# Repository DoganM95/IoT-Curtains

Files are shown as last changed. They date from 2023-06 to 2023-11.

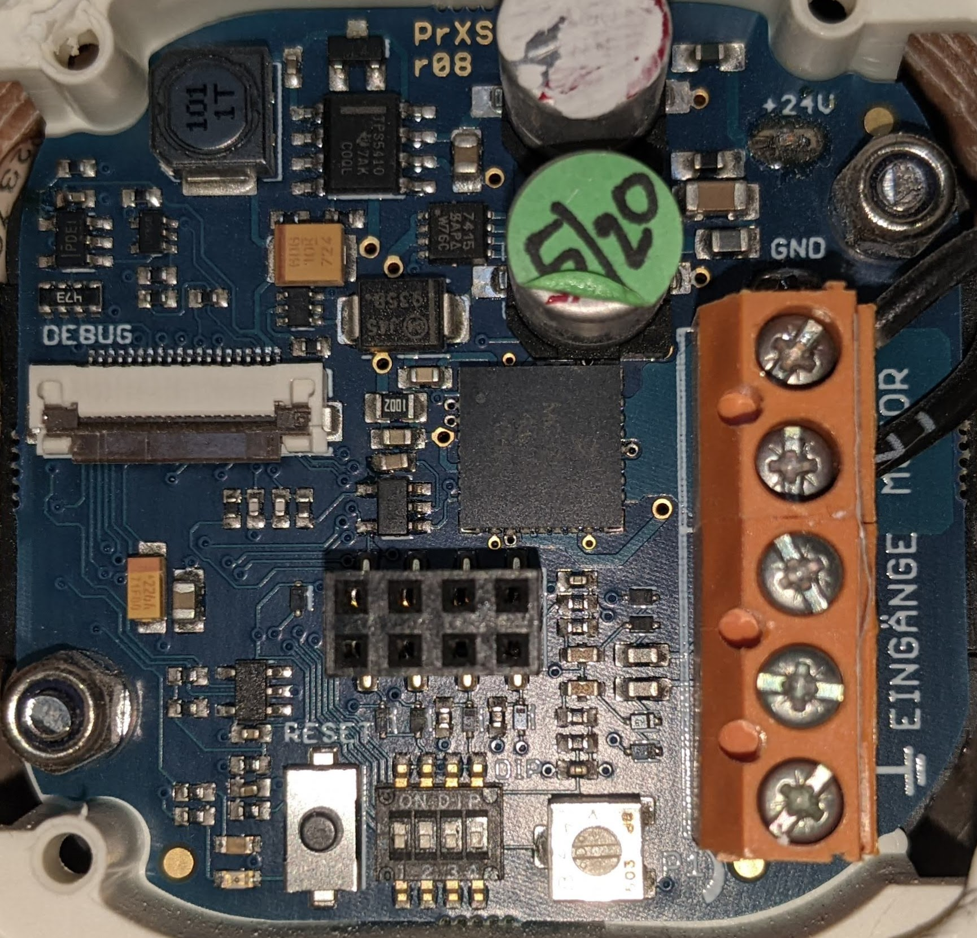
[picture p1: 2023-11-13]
Hardware/assets/wallmodule.png

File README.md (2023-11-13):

# IoT-Curtains
Outer facade electric curtains controlled by an esp32/arduino using Blynk
### Curtain controller pcb (wall module below)

- Pinout of screw spots:  

    Pin 5: Motor  
    Pin 4: Motor  
    Pin 3: close curtains  
    Pin 2: open curtains  
    Pin 1: GND  

- shorting pin 1 and pin 2 opens the curtains  
- shorting pin 1 and pin 3 closes the curtains  
- Pinout of female header pins (Wall side):

#### Power

The wall pcb provides power, rated at 3.3 Volts, but drops with increasing current draw.
The esp32 can be powered with a voltage between 2.2V and 3.6V and supposedly draws max 0.26A (Wifi Tx).
The following table contains measurements of voltage, respective to the current drawn at that moment.

<table>
  <tr>
    <td width="30%">
- 0.0A -> 3.31V<br/>  
- 0.1A -> 3.13V<br/>  
- 0.2A -> 2.93V<br/>  
- 0.3A -> 2.74V<br/>  
- 0.4A -> 2.55V<br/>  
- 0.5A -> 2.37V<br/>      
    </td>
    <td width="50%">USB-C PCB Bottom View</td>
  </tr>
</table>

### Hardware setup

- Shorting pins (1 and 2) && (1 and 3) by esp32 happens using AO3401A or AO3400A Mosfet, where esp controls the gate
- Mosfet Gate is connected to esp32 gpio (open/close)
- Mosfet gate is pulled down using a 10 kOhm resistor, connected from gate to ground
- pin 1 is connected to each Mosfet Source/Drain, depending on the diode direction of your mosfet (compare the 2 above in datasheets)
- pin 2/3 are each connected to a Source/Drain
- gpio will be high for a short time (e.g. 0.5s) to simulate a human button press

#### Existing wall module
This is the controller board that is built in to the wall. The wires of the motors of the facade are routed trough the wall and connected to it using the screw terminals. This module stays as is.
<table>
  <tr>
<td width="50%">Wall module</td>
    <td width="50%">Wall module labeled</td>
  </tr>
</table>

#### Preview of retrofitting smart module
This is the smart-module built in this project, which attaches to the wall-module above. It replaces the simple stock pcb that was attached to the wall module by default and only provided two led's (green/red) and two buttons (open/close).
<table>
  <tr>
<td width="50%">USB-C PCB Bottom View</td>
    <td width="50%">USB-C PCB Bottom View</td>
  </tr>
</table>

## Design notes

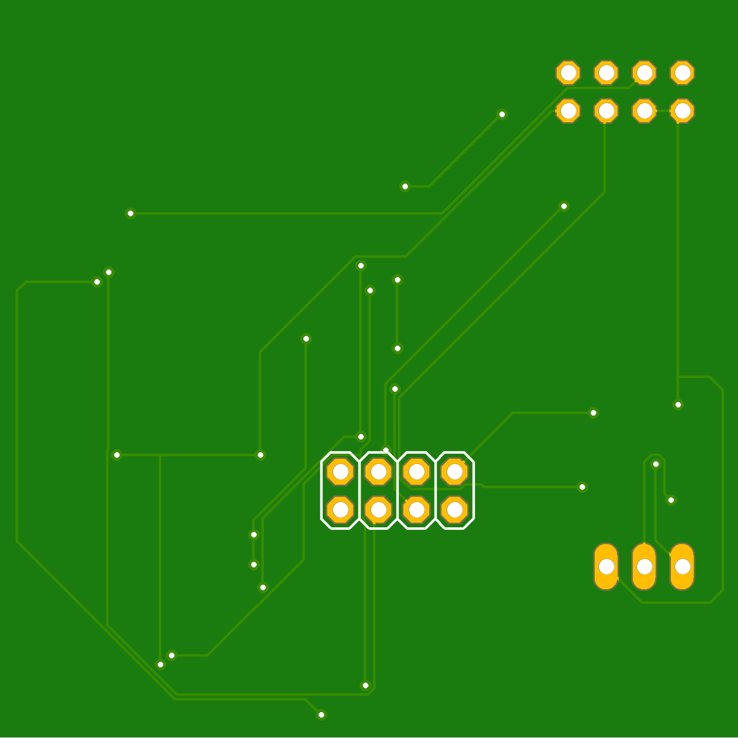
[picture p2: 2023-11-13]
Hardware/assets/curtains_bottom.png

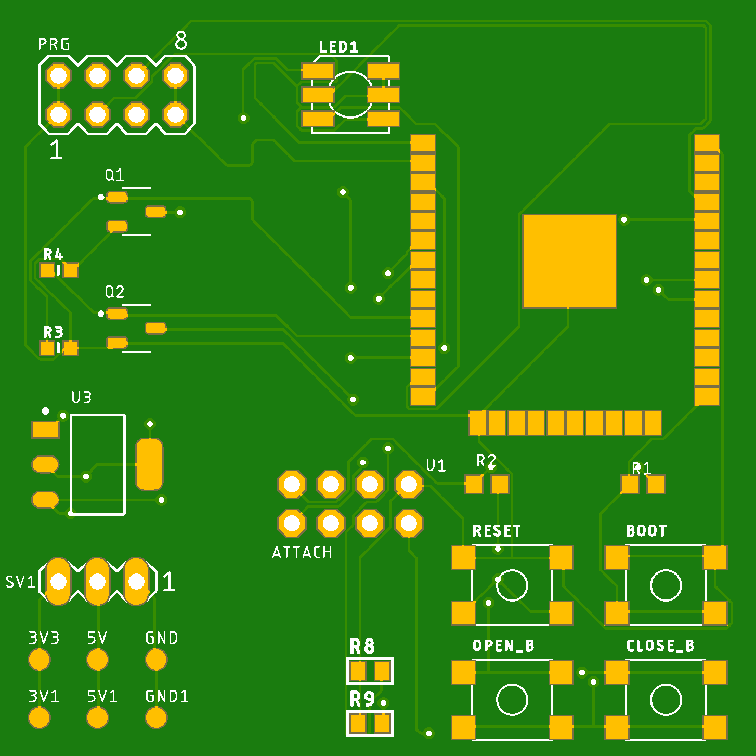
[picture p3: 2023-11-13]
Hardware/assets/curtains_top.png

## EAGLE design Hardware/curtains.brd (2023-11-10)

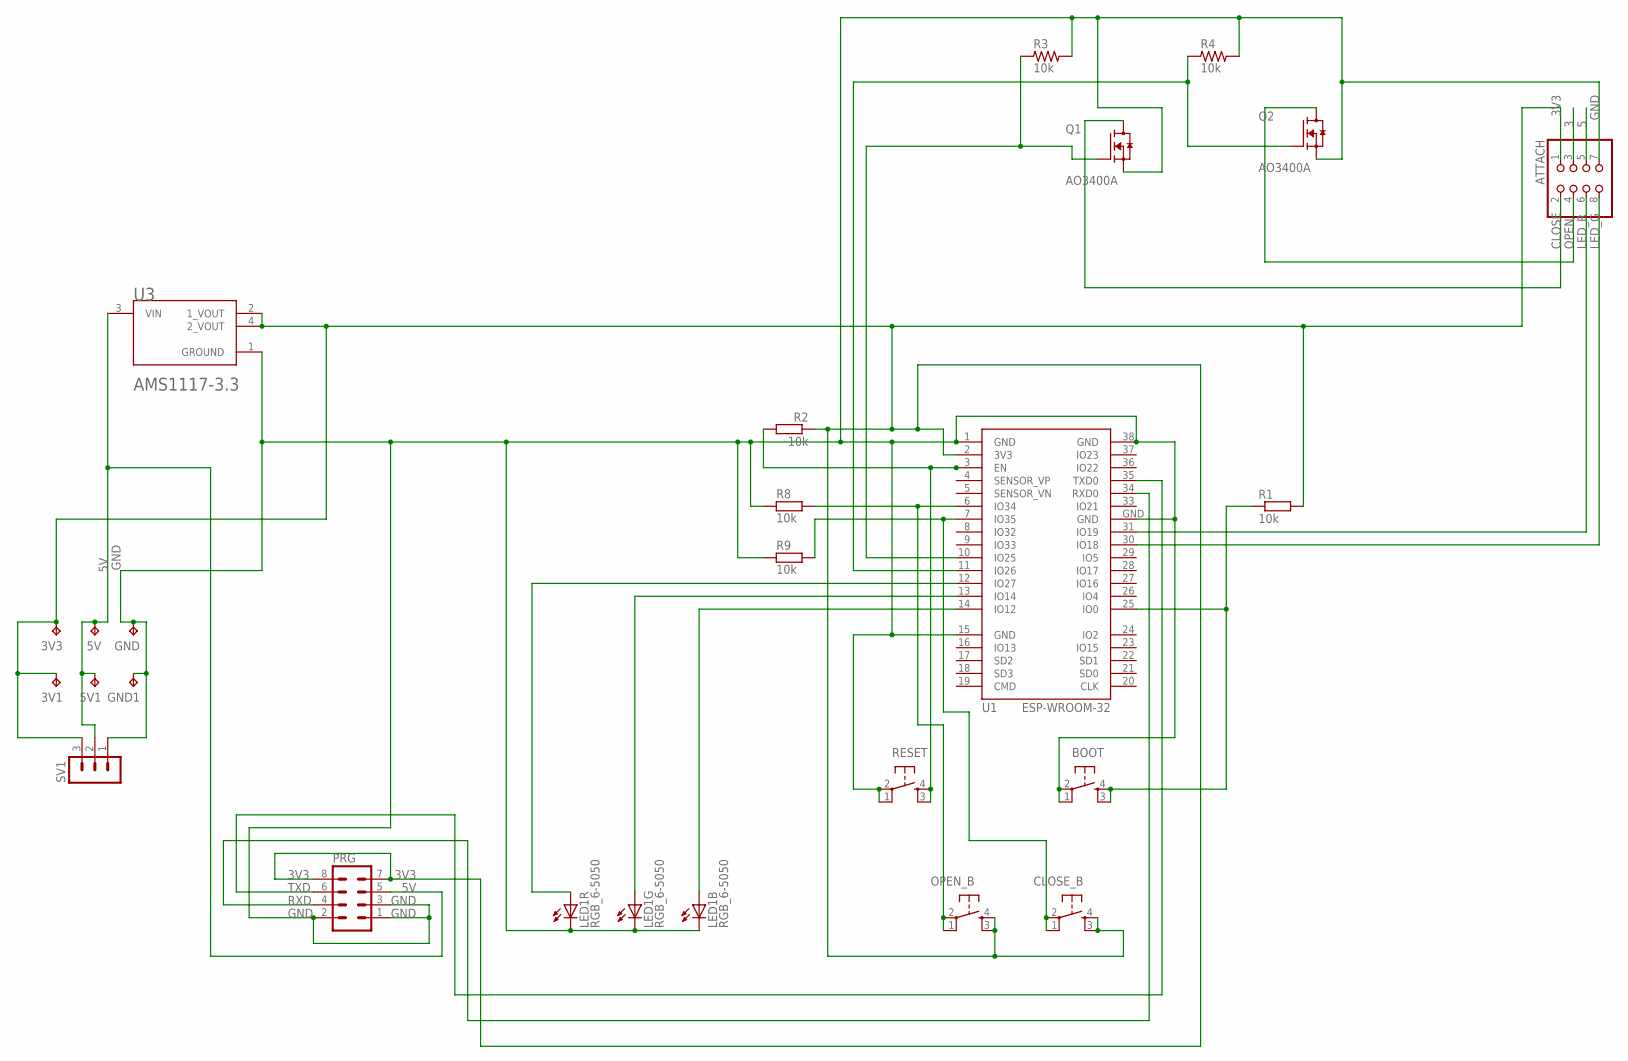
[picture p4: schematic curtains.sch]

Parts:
3V1, 3V3, 5V, 5V1: TPB1,27; B1,27
ATTACH: PINHD-2X4; 2X04
BOOT: 10-XX4X4SMD; BT4X4
CLOSE_B: 10-XX4X4SMD; BT4X4
GND, GND1: TPB1,27; B1,27
LED1: RGB_6-5050; 5050_PLCC6
OPEN_B: 10-XX4X4SMD; BT4X4
PRG: MA04-2
Q1, Q2: AO3400A; SOT95P280X125-3N
R1, R2, R8, R9: 10k; R0603
R3, R4: 10k; RC-MASTER-SMD_R0603MP
RESET: 10-XX4X4SMD; BT4X4
SV1: MA03-1
U1: ESP-WROOM-32
U3: ADVANCED_MONOLITHIC_SYSTEMS_AMS1117-3.3ADVANCED_M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; ADVANCED_MONOLITHIC_SYSTEMS_AMS1117-3.3_0

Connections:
3: ATTACH.3
3V3: 3V1.TP, 3V3.TP, ATTACH.1, CLOSE_B.3 (S1), CLOSE_B.4 (S), OPEN_B.3 (S1), OPEN_B.4 (S), PRG.7, PRG.8, R1.2, R2.1, SV1.3, U1.2 (3V3), U3.2 (1_VOUT), U3.4 (2_VOUT)
5: ATTACH.5
5V: 5V.TP, 5V1.TP, PRG.5, SV1.2, U3.3 (VIN)
CLOSE: ATTACH.2, Q1.3 (D)
GND: ATTACH.7, BOOT.1, BOOT.2, GND.TP, GND1.TP, LED1.4 (C), LED1.5 (C), LED1.6 (C), PRG.1, PRG.2, PRG.3, Q1.2 (S), Q2.2 (S), R3.2, R4.2, R8.1, R9.1, RESET.1, RESET.2, SV1.1, U1.1 (GND), U1.15 (GND), U1.38 (GND), U1.GND, U3.1 (GROUND)
LED_G: ATTACH.8, U1.30 (IO18)
LED_R: ATTACH.6, U1.31 (IO19)
unnamed: BOOT.3 (S1), BOOT.4 (S), R1.1, U1.25 (IO0)
unnamed: OPEN_B.1, OPEN_B.2, R8.2, U1.6 (IO34)
unnamed: R2.2, RESET.3 (S1), RESET.4 (S), U1.3 (EN)
unnamed: Q1.1 (G), R3.1, U1.10 (IO25)
unnamed: Q2.1 (G), R4.1, U1.11 (IO26)
unnamed: LED1.2 (A), U1.13 (IO14)
unnamed: LED1.3 (A), U1.14 (IO12)
unnamed: CLOSE_B.1, CLOSE_B.2, R9.2, U1.7 (IO35)
unnamed: LED1.1 (A), U1.12 (IO27)
OPEN: ATTACH.4, Q2.3 (D)
RXD: PRG.4, U1.34 (RXD0)
TXD: PRG.6, U1.35 (TXD0)

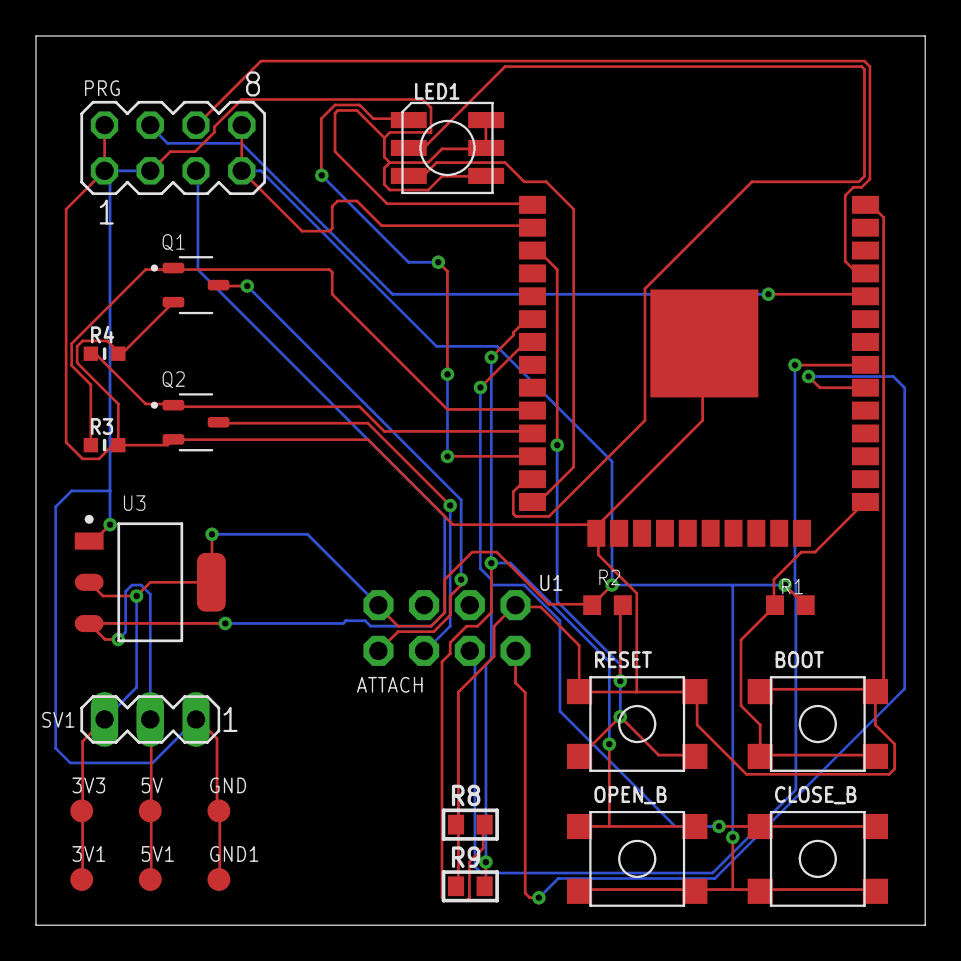
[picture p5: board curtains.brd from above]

Board: 2 copper layers, 49.4 x 49.4 mm, 24 parts (1 on the bottom side), 18 nets.

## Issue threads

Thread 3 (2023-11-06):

Fix manual buttons

DoganM95, 2023-11-06:
Test by cutting traces on existing board, wiring them to vcc and co figuring the io pins to input. Add 10k pulldowns, so the buttons don't trigger randomly. Then  add serial printf's to button pushes to debug when it triggers (could be a loop bug)

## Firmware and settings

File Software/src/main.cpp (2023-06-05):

// Configurations
#include "./Configuration/Blynk.h"
#include "./Configuration/Wifi.h"

// Libraries
#include <BlynkSimpleEsp32.h>  // Part of Blynk by Volodymyr Shymanskyy
#include <WiFi.h>              // Part of WiFi Built-In by Arduino
#include <WiFiClient.h>        // Part of WiFi Built-In by Arduino
#include <math.h>

#include <future>

// Configurations
const u_int pressDuration = 500;  // time the gpio should be HIGH, before it goes back to LOW
u_int ledBrightness = 4;          // between 0 and 255, respective to 0 to 100 %

// GPIO pins
const u_short openCurtainsPin = 26;   // Put a pulldown resistor on this one (10 kOhm from gpio -> GND)
const u_short closeCurtainsPin = 25;  // Put a pulldown resistor on this one (10 kOhm from gpio -> GND)

const u_short openCurtainsPhysicalButtonPin = 34;
const u_short closeCurtainsPhysicalButtonPin = 35;

const u_short ledRedPin = 14;
const u_short ledGreenPin = 12;
const u_short ledBluePin = 27;  // Workaround/fix for current iteration: jmp R5, omit R6 and R7

const u_short ledRedWallPin = 19;
const u_short ledGreenWallPin = 18;

// Limits
const int wifiHandlerThreadStackSize = 10000;
const int blynkHandlerThreadStackSize = 10000;

// Counters
unsigned long long wifiReconnectCounter = 0;
unsigned long long blynkReconnectCounter = 0;

// Timeouts
int wifiConnectionTimeout = 10000;
int blynkConnectionTimeout = 10000;
int blynkConnectionStabilizerTimeout = 5000;
ushort cycleDelayInMilliSeconds = 100;

// Task Handles
TaskHandle_t wifiConnectionHandlerThreadFunctionHandle;
TaskHandle_t blynkConnectionHandlerThreadFunctionHandle;
TaskHandle_t buttonSensorThreadFunctionHandle;
TaskHandle_t redWallLedSensorThreadFunctionHandle;
TaskHandle_t greenWallLedSensorThreadFunctionHandle;
TaskHandle_t blueLedThreadFunctionHandle;

// Declarations
void blynkConnectionHandlerThreadFunction(void* params);
void wifiConnectionHandlerThreadFunction(void* params);
void buttonSensorThread(void* params);
void pressButton(u_short pin, u_int durationInMs);
void redWallLedSensorThread(void* params);
void greenWallLedSensorThread(void* params);
void blueLedThread(void* params);

// Led Colors
class led {
 public:
  inline static std::array<int, 3> black = {0, 0, 0};
  inline static std::array<int, 3> red = {1, 0, 0};
  inline static std::array<int, 3> green = {0, 1, 0};
  inline static std::array<int, 3> blue = {0, 0, 1};
  inline static std::array<int, 3> yellow = {1, 1, 0};
  inline static std::array<int, 3> magenta = {1, 0, 1};
  inline static std::array<int, 3> cyan = {0, 1, 1};
  inline static std::array<int, 3> white = {1, 1, 1};

  inline static std::array<int, 3> lastColor = {0, 0, 0};
  inline static std::array<int, 3> previousColor = {0, 0, 0};

  static std::future<void> setColorAsync(const std::array<int, 3>& color, u_int durationInMs) {
    return std::async(std::launch::async, [=]() {
      led::previousColor = led::lastColor;  // Save the last color before changing it
      led::lastColor = color;
      analogWrite(ledRedPin, color[0] * ledBrightness);
      analogWrite(ledGreenPin, color[1] * ledBrightness);
      analogWrite(ledBluePin, color[2] * ledBrightness);
      delay(durationInMs);
    });
  }

  static std::future<void> addColorAsync(const std::array<int, 3>& color, u_int durationInMs) {
    return std::async(std::launch::async, [=]() {
      const int ledPins[] = {ledRedPin, ledGreenPin, ledBluePin};
      for (int i = 0; i < 3; ++i) {
        if (color[i] == 1) {
          analogWrite(ledPins[i], color[i] * ledBrightness);
        }
      }
      delay(durationInMs);
    });
  }

  static std::future<void> removeColorAsync(const std::array<int, 3>& color) {
    return std::async(std::launch::async, [=]() {
      const int ledPins[] = {ledRedPin, ledGreenPin, ledBluePin};
      for (int i = 0; i < 3; ++i) {
        if (color[i] == 1) {
          analogWrite(ledPins[i], 0);
        }
      }
    });
  }

  static void setPreviousColor() {
    analogWrite(ledRedPin, previousColor[0] * ledBrightness);
    analogWrite(ledGreenPin, previousColor[1] * ledBrightness);
    analogWrite(ledBluePin, previousColor[2] * ledBrightness);
  }

  static void setBrightness(u_int brightness) {
    ledBrightness = brightness;
    led::setColorAsync(led::lastColor, 0).get();
  }
};

// SETUP
void setup() {
  Serial.begin(115200);

  pinMode(openCurtainsPin, OUTPUT);
  pinMode(closeCurtainsPin, OUTPUT);

  pinMode(openCurtainsPhysicalButtonPin, INPUT);
  pinMode(closeCurtainsPhysicalButtonPin, INPUT);

  pinMode(ledRedWallPin, INPUT_PULLDOWN);
  pinMode(ledGreenWallPin, INPUT_PULLDOWN);

  pinMode(ledRedPin, OUTPUT);
  pinMode(ledGreenPin, OUTPUT);
  pinMode(ledBluePin, OUTPUT);

  led::setColorAsync(led::red, 1000).get();
  led::setColorAsync(led::green, 1000).get();
  led::setColorAsync(led::blue, 1000).get();
  led::setColorAsync(led::black, 0).get();

  xTaskCreatePinnedToCore(wifiConnectionHandlerThreadFunction, "Wifi Connection Handling Thread", wifiHandlerThreadStackSize, NULL, 20, &wifiConnectionHandlerThreadFunctionHandle, 1);
  xTaskCreatePinnedToCore(blynkConnectionHandlerThreadFunction, "Blynk Connection Handling Thread", blynkHandlerThreadStackSize, NULL, 20, &blynkConnectionHandlerThreadFunctionHandle, 1);
  // TODO: reactivate in bug-fixed pcb iteration, where button pin is connected to 3v3 instead of ground...
  // xTaskCreatePinnedToCore(buttonSensorThread, "Physical Button Sensing Thread", 10000, NULL, 20, &buttonSensorThreadFunctionHandle, 0);
  xTaskCreatePinnedToCore(redWallLedSensorThread, "Red Wall Led Sensor Thread", 10000, NULL, 20, &redWallLedSensorThreadFunctionHandle, 0);
  xTaskCreatePinnedToCore(greenWallLedSensorThread, "Green Wall Led Sensor Thread", 10000, NULL, 20, &greenWallLedSensorThreadFunctionHandle, 0);
  xTaskCreatePinnedToCore(blueLedThread, "Blue Led Thread", 10000, NULL, 20, &blueLedThreadFunctionHandle, 0);
}

// MAIN LOOP
void loop() { Blynk.run(); }

// FUNCTIONS

BLYNK_CONNECTED() {  // Restore hardware pins according to current UI config
  Blynk.syncAll();
}

BLYNK_WRITE(V0) {  // Open curtains
  int pinValue = param.asInt();
  led::setBrightness(pinValue);
}

BLYNK_WRITE(V1) {  // Open curtains
  int pinValue = param.asInt();
  if (pinValue == 1) pressButton(openCurtainsPin, pressDuration);
}

BLYNK_WRITE(V2) {  // Set led brightness
  int pinValue = param.asInt();
  if (pinValue == 1) pressButton(closeCurtainsPin, pressDuration);
}

void redWallLedSensorThread(void* param) {
  bool isLastColorRestored = true;
  while (true) {
    if (digitalRead(ledRedWallPin) == HIGH) {
      led::addColorAsync(led::red, 0).get();
      while (digitalRead(ledRedWallPin)) {
        delay(10);
      }
      isLastColorRestored = false;
    }
    if (digitalRead(ledRedWallPin) == LOW && isLastColorRestored == false) {
      led::removeColorAsync(led::red).get();
      isLastColorRestored = true;
    }
    delay(10);
  }
}

void greenWallLedSensorThread(void* param) {
  bool isLastColorRestored = true;
  while (true) {
    if (digitalRead(ledGreenWallPin) == HIGH) {
      led::addColorAsync(led::green, 0).get();
      while (digitalRead(ledGreenWallPin) == HIGH) {
        delay(10);
      }
      isLastColorRestored = false;
    }
    if (digitalRead(ledGreenWallPin) == LOW && isLastColorRestored == false) {
      led::removeColorAsync(led::green).get();
      isLastColorRestored = true;
    }
    delay(10);
  }
}

void blueLedThread(void* param) {
  bool isLastColorRestored = true;
  while (true) {
    if (Blynk.connected() && WiFi.isConnected()) {
      led::addColorAsync(led::blue, 0).get();
    } else {
      while (!Blynk.connected() || !WiFi.isConnected()) {
        led::addColorAsync(led::blue, 0).get();
        delay(500);
        led::removeColorAsync(led::blue).get();
      }
    }
    delay(10);
  }
}

void buttonSensorThread(void* params) {
  while (true) {
    if (digitalRead(openCurtainsPhysicalButtonPin) == HIGH) {
      pressButton(openCurtainsPin, pressDuration);  // blocks this loop for pressDuration, serves as debounce
    }
    if (digitalRead(closeCurtainsPhysicalButtonPin) == HIGH) {
      pressButton(closeCurtainsPin, pressDuration);  // blocks this loop for pressDuration, serves as debounce
    }
    delay(10);  // Lessen cpu usage
  }
}

void pressButton(u_short pin, u_int durationInMs) {
  digitalWrite(pin, 1);
  delay(durationInMs);  // also serves as a debounce delay for the physical button
  digitalWrite(pin, 0);
  Serial.printf("Button %d pressed\n", pin);
}

void WaitForWifi(uint cycleDelayInMilliSeconds) {
  while (WiFi.status() != WL_CONNECTED) {
    delay(cycleDelayInMilliSeconds);
  }
}

void WaitForBlynk(int cycleDelayInMilliSeconds) {
  while (!Blynk.connected()) {
    delay(cycleDelayInMilliSeconds);
  }
}

void wifiConnectionHandlerThreadFunction(void* params) {
  uint time;
  while (true) {
    if (!WiFi.isConnected()) {
      try {
        Serial.printf("Connecting to Wifi: %s\n", WIFI_SSID);
        WiFi.begin(WIFI_SSID, WIFI_PW);  // initial begin as workaround to some espressif library bug
        WiFi.disconnect();
        WiFi.begin(WIFI_SSID, WIFI_PW);
        WiFi.setHostname("Desklight (ESP32, Blynk)");
        time = 0;
        while (WiFi.status() != WL_CONNECTED) {
          if (time >= wifiConnectionTimeout || WiFi.isConnected()) break;
          delay(cycleDelayInMilliSeconds);
          time += cycleDelayInMilliSeconds;
        }
      } catch (const std::exception e) {
        Serial.printf("Error occured: %s\n", e.what());
      }
      if (WiFi.isConnected()) {
        Serial.printf("Connected to Wifi: %s\n", WIFI_SSID);
        wifiReconnectCounter = 0;
      }
    }
    delay(1000);
    // Serial.printf("Wifi Connection Handler Thread current stack size: %d , current Time: %d\n", wifiHandlerThreadStackSize - uxTaskGetStackHighWaterMark(NULL), xTaskGetTickCount());
  };
}

void blynkConnectionHandlerThreadFunction(void* params) {
  uint time;
  while (true) {
    if (!Blynk.connected()) {
      Serial.printf("Connecting to Blynk: %s\n", BLYNK_USE_LOCAL_SERVER == true ? BLYNK_SERVER : "Blynk Cloud Server");
      if (BLYNK_USE_LOCAL_SERVER)
        Blynk.config(BLYNK_AUTH, BLYNK_SERVER, BLYNK_PORT);
      else
        Blynk.config(BLYNK_AUTH);
      Blynk.connect();  // Connects using the chosen Blynk.config
      uint time = 0;
      while (!Blynk.connected()) {
        if (time >= blynkConnectionTimeout || Blynk.connected()) break;
        delay(cycleDelayInMilliSeconds);
        time += cycleDelayInMilliSeconds;
      }
      if (Blynk.connected()) {
        Serial.printf("Connected to Blynk: %s\n", BLYNK_USE_LOCAL_SERVER ? BLYNK_SERVER : "Blynk Cloud Server");
        delay(blynkConnectionStabilizerTimeout);
      }
    }
    delay(1000);
    // Serial.printf("Blynk Connection Handler Thread current stack size: %d , current Time: %d\n", blynkHandlerThreadStackSize - uxTaskGetStackHighWaterMark(NULL), xTaskGetTickCount());
  }
}

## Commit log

2022-05-13 untested initital prototype
2022-06-03 fix for every day use
    [Sketch.ino]
2022-12-23 add pcb files
    [curtains.brd, curtains.sch]
2022-12-23 add schematics to readme
2022-12-23 prioritize schematic
2022-12-28 add gerber files from pcb design
2023-01-19 restructure for platformio
    [curtains.brd, curtains.sch]
2023-05-06 turn into platformio project
    [curtains.brd, curtains.sch]
2023-05-31 add gerber files for v2
2023-06-02 add led color func, button sense thread & todos
2023-06-04 implement wall led sensor
2023-06-04 add more led stuff
2023-06-04 fix green led restore bug
    [main.cpp]
2023-11-10 restructure to have soft and hardware
    [curtains.brd, curtains.sch]

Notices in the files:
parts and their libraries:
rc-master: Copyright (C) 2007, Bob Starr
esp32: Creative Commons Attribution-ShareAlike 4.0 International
